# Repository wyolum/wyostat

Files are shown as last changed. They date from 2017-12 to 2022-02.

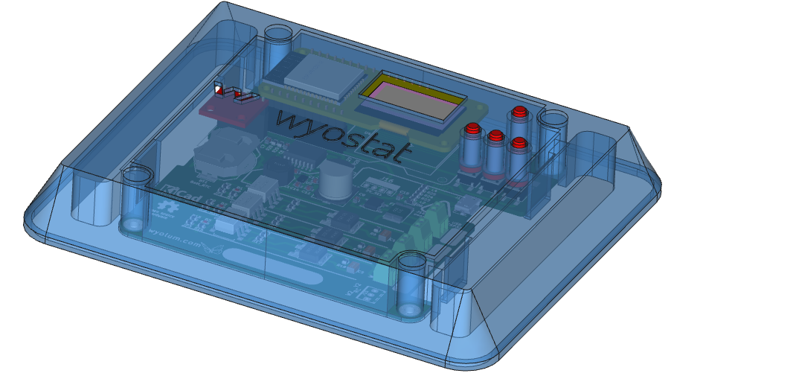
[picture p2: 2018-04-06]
fabricate/images/wyostat_fab_05.png

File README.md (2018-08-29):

# wyostat
Open source thermostat

* install node-red
           * https://nodered.org/docs/hardware/raspberrypi
* install node-red-dashboard
   	   * (from the ~/.node-red)
	   * https://flows.nodered.org/node/node-red-dashboard
* install node-red start up trigger: npm install node-red-contrib-startup-trigger
* install mosquitto (steps 1 & 2
           *https://learn.adafruit.com/diy-esp8266-home-security-with-lua-and-mqtt/configuring-mqtt-on-the-raspberry-pi)
* start node-red (from the command-line type $node-red)
* start mosquitto (from the command line type $moquitto)
* edit OpenThermostat.json from within node-red (update mqtt-broker ip address)
* deploy OpenThermostat.json from within node-red (update mqtt-broker ip address)
* Copy and edit arduino/OpenThermostat/README to arduino/OpenThermostat/config.h
* upload OpenThermostat.ino

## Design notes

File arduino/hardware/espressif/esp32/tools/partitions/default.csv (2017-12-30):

# Name | Type | SubType | Offset | Size | Flags
nvs | data | nvs | 0x9000 | 0x5000
otadata | data | ota | 0xe000 | 0x2000
app0 | app | ota_0 | 0x10000 | 0x140000
app1 | app | ota_1 | 0x150000 | 0x140000
eeprom | data | 0x99 | 0x290000 | 0x1000
spiffs | data | spiffs | 0x291000 | 0x16F000

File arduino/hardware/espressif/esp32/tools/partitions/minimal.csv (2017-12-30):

# Name | Type | SubType | Offset | Size | Flags
nvs | data | nvs | 0x9000 | 0x5000
otadata | data | ota | 0xe000 | 0x2000
app0 | app | ota_0 | 0x10000 | 0x140000
eeprom | data | 0x99 | 0x150000 | 0x1000
spiffs | data | spiffs | 0x151000 | 0xAF000

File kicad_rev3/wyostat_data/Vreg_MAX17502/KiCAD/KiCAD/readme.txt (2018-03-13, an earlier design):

 

**********************************************************
*************  Important Instructions Follow  ************
**********************************************************
 
All files exported to: C:\EMA\ExportFolder\0\175637\Output\KiCAD\KiCAD\symbols.lib

After you have used Ultra Librarian to export library:
**************************************************
**To import your new library symbols into KiCad:**
**************************************************
1. Open KiCad.
2. On the program/tool list, go to Eeschema.
3. Select *Preferences* from the menu bar then select *Library*.
4. Click *Add* and choose the newly exported *.LIB* file.
5. You have now successfully imported your new symbol library!

**************************************************************
**To import your new library footprints/patterns into KiCad:**
**************************************************************
1. Open KiCad.
2. On the program/tool list, go to Pcbnew.
3. Follow the same steps as you would importing symbols, only this time select the *.kicad_mod* file.
4. You have now successfully imported your new footprint/pattern.

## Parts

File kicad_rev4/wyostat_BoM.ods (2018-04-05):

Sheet: wyostat_pcb_BoM
No | Designator | Package | Quantity | Designation | Digi PN | Mfr. | Mfg PN | Decription | Link
1 | BT1 | CR2032_SMD | 1 | Batt_RTC | BK-912-ND | MPD (Memory Protection Devices) | BK-912 | HOLDER COIN CELL 20MM SMD | https://www.digikey.com/product-detail/en/mpd-memory-protection-devices/BK-912/BK-912-ND/2647825
2 | BATT1 | CR2032 | 1 | Battery Coin 2032 | P189-ND | Panasonic – BSG | CR2032 | BATTERY LITHIUM 3V COIN 20MM | https://www.digikey.com/product-detail/en/panasonic-bsg/CR2032/P189-ND/31939
3 | C1,C3,C5 | C_1210 | 3 | 10nF,120V | 399-12880-1-ND | KEMET | LDEIB2100KA0N00 | CAP FILM 10000PF 10% 250VDC 1210 | https://www.digikey.com/product-detail/en/kemet/LDEIB2100KA0N00/399-12880-1-ND/5731504
4 | C7,C8 | C_0805 | 2 | 100nF | 490-8049-1-ND | Murata Electronics North America | GCM21BR71H104KA37K | CAP CER 0.1UF 50V X7R 0805 | https://www.digikey.com/scripts/DkSearch/dksus.dll?Detail&itemSeq=255949432&uq=636584419937553153
5 | C9 | C_0805 | 1 | 100nF,100V | 1276-6733-1-ND | Samsung Electro-Mechanics | GCM21BR71H104KA37K | CAP CER 0.1UF 100V X7R 0805 | https://www.digikey.com/product-detail/en/samsung-electro-mechanics/CL21B104KCFWPNE/1276-6733-1-ND/5961592
6 | C10 | CP_Elec_10x10 | 1 | 100uF,50V | 565-4786-1-ND | United Chemi-Con | HHXC500ARA101MJA0G | CAP ALUM POLY 100UF 20% 50V SMD | https://www.digikey.com/product-detail/en/united-chemi-con/HHXC500ARA101MJA0G/565-4786-1-ND/7556757
7 | C11 | C_0805 | 1 | 2.2uF,50V | 587-4963-1-ND | Taiyo Yuden | UMK212BB7225MG-T | CAP CER 2.2UF 50V X7R 0805 | https://www.digikey.com/product-detail/en/taiyo-yuden/UMK212BB7225MG-T/587-4963-1-ND/6563806
8 | C12 | C_0805 | 1 | 1uF | 1276-1029-1-ND | Samsung Electro-Mechanics | CL21B105KBFNNNE | CAP CER 1UF 50V X7R 0805 | https://www.digikey.com/product-detail/en/samsung-electro-mechanics/CL21B105KBFNNNE/1276-1029-1-ND/3889115
9 | C13 | C_0805 | 1 | 3.3nF | 399-1153-1-ND | KEMET | C0805C332K5RACTU | CAP CER 3300PF 50V X7R 0805 | https://www.digikey.com/product-detail/en/kemet/C0805C332K5RACTU/399-1153-1-ND/411428
10 | C14 | C_0805 | 1 | 10uF | 587-3319-1-ND | Taiyo Yuden | EMK212BB7106MG-T | CAP CER 10UF 16V X7R 0805 | https://www.digikey.com/product-detail/en/taiyo-yuden/EMK212BB7106MG-T/587-3319-1-ND/4157364
11 | C15 | C_0805 | 1 | 4.7uF | 1276-2873-1-ND | Samsung Electro-Mechanics | CL21B475KOFNNNE | CAP CER 4.7UF 16V X7R 0805 | https://www.digikey.in/product-detail/en/samsung-electro-mechanics/CL21B475KOFNNNE/1276-2873-1-ND/3890959
12 | D1,D2,D3 | LED_0603 | 3 | LED | 160-1828-1-ND | Lite-On Inc. | LTST-C193KGKT-5A | LED GREEN CLEAR 0603 SMD | https://www.digikey.com/product-detail/en/lite-on-inc/LTST-C193KGKT-5A/160-1828-1-ND/2356247
13 | D4 | Diode_bridge | 1 | DiodeBridge | MDB6SFSCT-ND | ON Semiconductor | MDB6S | IC BRIDGE DIODE 600V 4-MICRODIP | https://www.digikey.com/product-detail/en/on-semiconductor/MDB6S/MDB6SFSCT-ND/3137112
14 | D5 | D_SOD-323_HandSoldering | 1 | CDSOD323-T05L | CDSOD323-T05LCT-ND | Bourns Inc. | CDSOD323-T05L | TVS DIODE 5V 18.3V SOD323 | https://www.digikey.com/product-detail/en/bourns-inc/CDSOD323-T05L/CDSOD323-T05LCT-ND/5355715
15 | F1 | Fuse_SMD2920 | 1 | Polyfuse | 507-1743-1-ND | Bel Fuse Inc. | 0ZCF0075AF2C | PTC RESET FUSE 60V 750MA 2920 | https://www.digikey.com/product-detail/en/bel-fuse-inc/0ZCF0075AF2C/507-1743-1-ND/4156174
16 | J1,J2,J3,J4 | TerminalBlock_Pheonix_MPT-2.54mm_2pol | 4 | 24VAC IN,OUT1,OUT2,OUT3 | A98333-ND | TE Connectivity AMP Connectors | 282834-2 | TERM BLOCK 2POS SIDE ENT 2.54MM | https://www.digikey.com/product-detail/en/te-connectivity-amp-connectors/282834-2/A98333-ND/1150135
17 | J13 | USB_Micro-B_Molex-105017-0001 | 1 | USB_microAB | WM1399CT-ND | Molex, LLC | 1050170001 | CONN RCPT MICRO USB R/A SMD | https://www.digikey.com/product-detail/en/molex-llc/1050170001/WM1399CT-ND/2350885
18 | J16 | Pin_Header_Straight_1x04 | 1 | 5V_SEL | S1011EC-04-ND | Sullins Connector Solutions | PRPC004SAAN-RC | CONN HEADER .100" SNGL STR 4POS | https://www.digikey.com/product-detail/en/sullins-connector-solutions/PRPC004SAAN-RC/S1011EC-04-ND/2775250
19 | JP1,JP2,JP3 | R_0805 | 3 | LED_en | YAG3755CT-ND | Yageo | AC0805JR-070RL | RES SMD 0 OHM JUMPER 1/8W 0805 | https://www.digikey.com/product-detail/en/yageo/AC0805JR-070RL/YAG3755CT-ND/6006604
20 | Shorting link for J16 | -- | 1 | -- | S9337-ND | Sullins Connector Solutions | QPC02SXGN-RC | CONN JUMPER SHORTING .100" GOLD | https://www.digikey.com/product-detail/en/sullins-connector-solutions/QPC02SXGN-RC/S9337-ND/2618262
21 | L1 | Inductor_ELL8TP | 1 | 22uH | PCD2446CT-ND | Panasonic Electronic Components | ELL-8TP220MB | FIXED IND 22UH 2A 55 MOHM SMD | https://www.digikey.com/product-detail/en/panasonic-electronic-components/ELL-8TP220MB/PCD2446CT-ND/5673833
22 | L2,L4 | R_0805 | 2 | 330E | 445-1569-1-ND | TDK Corporation | MPZ2012S331AT000 | FERRITE BEAD 330 OHM 0805 1LN | https://www.digikey.com/product-detail/en/tdk-corporation/MPZ2012S331AT000/445-1569-1-ND/571899
23 | Q1,Q2,Q3 | DPAK-2 | 3 | BTA204S | 1740-1106-1-ND | WeEn Semiconductors | BTA204S-600E,118 | TRIAC SENS GATE 600V 4A DPAK | https://www.digikey.com/product-detail/en/ween-semiconductors/BTA204S-600E118/1740-1106-1-ND/2531110
24 | R1,R5,R7,R12,R13,R17 | R_0805 | 6 | 360 | 311-360CRCT-ND | Yageo | RC0805FR-07360RL | RES SMD 360 OHM 1% 1/8W 0805 | https://www.digikey.com/product-detail/en/yageo/RC0805FR-07360RL/311-360CRCT-ND/730833
25 | R3,R9,R15 | R_0805 | 3 | 200 | 311-200ARCT-ND | Yageo | RC0805JR-07200RL | RES SMD 200 OHM 5% 1/8W 0805 | https://www.digikey.com/product-detail/en/yageo/RC0805JR-07200RL/311-200ARCT-ND/731226
26 | R4,R10,R16 | R_0805 | 3 | 300 | 311-300ARCT-ND | Yageo | RC0805JR-07300RL | RES SMD 300 OHM 5% 1/8W 0805 | https://www.digikey.com/product-detail/en/yageo/RC0805JR-07300RL/311-300ARCT-ND/731254
27 | R6,R11,R18 | R_0805 | 3 | 39 | 311-39ARCT-ND | Yageo | RC0805JR-0739RL | RES SMD 39 OHM 5% 1/8W 0805 | https://www.digikey.com/product-detail/en/yageo/RC0805JR-0739RL/311-39ARCT-ND/731268
28 | R19,R20,R21,R22,R26,R27 | R_0805 | 6 | 10k | 311-10KARCT-ND | Yageo | RC0805JR-0710KL | RES SMD 10K OHM 5% 1/8W 0805 | https://www.digikey.com/product-detail/en/yageo/RC0805JR-0710KL/311-10KARCT-ND/731188
29 | R28,R29 | R_0805 | 2 | 4K7 | 311-4.70KCRCT-ND | Yageo | RC0805FR-074K7L | RES SMD 4.7K OHM 1% 1/8W 0805 | https://www.digikey.com/product-detail/en/yageo/RC0805FR-074K7L/311-4.70KCRCT-ND/730876
30 | S1,S2,S3,S4 | SW_SPST_FSM6JSMA | 4 | SW-ENTER,SW-INC,SW-DEC,SW-MODE | 450-1133-ND | TE Connectivity ALCOSWITCH Switches | FSM6JSMA | SWITCH TACTILE SPST-NO 0.05A 24V | https://www.digikey.com/product-detail/en/te-connectivity-alcoswitch-switches/FSM6JSMA/450-1133-ND/525822
31 | U1,U2,U3 | Optocoupler_6pin_smd | 3 | MOC3063M | MOC3063SR2MCT-ND | ON Semiconductor | MOC3063SR2M | OPTOISOLATOR 4.17KV TRIAC 6SMD | https://www.digikey.com/product-detail/en/on-semiconductor/MOC3063SR2M/MOC3063SR2MCT-ND/1626439
32 | U4 | Wemos_Lolin | 1 | Wemos-Lolin
33 | U5 | TDFN-10 | 1 | MAX17502FATB+T | MAX17502FATB+TCT-ND | Maxim Integrated | MAX17502FATB+T | IC REG BUCK 5V 1A SYNC 10TDFN | https://www.digikey.com/product-detail/en/maxim-integrated/MAX17502FATB-T/MAX17502FATB-TCT-ND/4807778
34 | U130 | DS3231 | 1 | DS3231N | DS3231M+-ND | Maxim Integrated | DS3231M+ | IC RTC CLK/CALENDAR I2C 16-SOIC | https://www.digikey.com/product-detail/en/maxim-integrated/DS3231M/DS3231M-ND/2402420

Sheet: BoM_SCH
Quantity | Reference | Value | DNP
1 | BT1, | Batt_RTC
3 | C1,C3,C5, | 10nF,120V
2 | C7,C8, | 100nF
1 | C9, | 100nF,100V
1 | C10, | 100uF,50V
1 | C11, | 2.2uF,50V
1 | C12, | 1uF
1 | C13, | 3.3nF
1 | C14, | 10uF
1 | C15, | 4.7uF
3 | D1,D2,D3, | LED
1 | D4, | DiodeBridge
1 | D5, | CDSOD323-T05L
1 | F1, | Polyfuse
1 | J1, | 24 V AC IN
1 | J2, | OUT1
1 | J3, | OUT2
1 | J4, | OUT3
1 | J13, | USB_microAB
1 | J16, | 5V_SEL
3 | JP1,JP2,JP3, | LED_en
1 | L1, | 22uH
2 | L2,L4, | 330E
3 | Q1,Q2,Q3, | BTA204S
6 | R1,R5,R7,R12,R13,R17, | 360
3 | R3,R9,R15, | 200
3 | R4,R10,R16, | 300
3 | R6,R11,R18, | 39 | -
6 | R19,R20,R21,R22,R26,R27, | 10k
2 | R28,R29, | 4K7
1 | S1, | SW-ENTER
1 | S2, | SW-INC
1 | S3, | SW-DEC
1 | S4, | SW-MODE
3 | U1,U2,U3, | MOC3063M
1 | U4, | Wemos-Lolin
1 | U5, | MAX17502FATB+T
1 | U6, | DS3231N
1 | J5, | I2C_ext1
1 | J6, | RH
1 | J7, | RC
1 | J8, | C
1 | J9, | Y1
1 | J10, | Y2
1 | J11, | G
1 | J12, | W1
1 | J14, | W2
1 | J15, | Conn_Spare
1 | JP4, | GND
1 | Logo1, | LOGO_WL
1 | Logo2, | OSHW
1 | Logo3, | KiCad
1 | Logo4, | logo_snb
1 | Logo5, | logo_warning
3 | R23,R24,R25, | 0E | DNP
4 | SC1,SC2,SC3,SC4, | SCREW
1 | TP1, | ~RST
1 | TP2, | SQR
1 | TP3, | 32kHz

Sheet: BoM_PCB
Id | Designator | Package | Quantity | Designation | Supplier and ref
1 | BT1 | CR2032_SMD2 | 1 | Batt_RTC
2 | C1,C3,C5 | C_1210 | 3 | 10nF,120V
3 | C7,C8 | C_0805 | 2 | 100nF
4 | C9 | C_0805 | 1 | 100nF,100V
5 | C10 | CP_Elec_10x10 | 1 | 100uF,50V
6 | C11 | C_0805 | 1 | 2.2uF,50V
7 | C12 | C_0805 | 1 | 1uF
8 | C13 | C_0805 | 1 | 3.3nF
9 | C14 | C_0805 | 1 | 10uF
10 | C15 | C_0805 | 1 | 4.7uF
11 | D1,D2,D3 | LED_0603 | 3 | LED
12 | D4 | Diode_bridge | 1 | DiodeBridge
13 | D5 | D_SOD-323_HandSoldering | 1 | CDSOD323-T05L
14 | F1 | Fuse_SMD2920 | 1 | Polyfuse
15 | J1 | TerminalBlock_Pheonix_MPT-2.54mm_2pol | 1 | 24 V AC IN
 | J2 | TerminalBlock_Pheonix_MPT-2.54mm_2pol | 1 | OUT1
 | J3 | TerminalBlock_Pheonix_MPT-2.54mm_2pol | 1 | OUT2
 | J4 | TerminalBlock_Pheonix_MPT-2.54mm_2pol | 1 | OUT3
16 | J13 | USB_Micro-B_Molex-105017-0001 | 1 | USB_microAB
17 | J16 | Pin_Header_Straight_1x04 | 1 | 5V_SEL
18 | JP1,JP2,JP3 | R_0805 | 3 | LED_en
19 | L1 | Inductor_ELL8TP | 1 | 22uH
20 | L2,L4 | R_0805 | 2 | 330E
21 | Q1,Q2,Q3 | DPAK-2 | 3 | BTA204S
22 | R1,R5,R7,R12,R13,R17 | R_0805 | 6 | 360
23 | R3,R9,R15 | R_0805 | 3 | 200
24 | R4,R10,R16 | R_0805 | 3 | 300
25 | R6,R11,R18 | R_0805 | 3 | 39
26 | R19,R20,R21,R22,R26,R27 | R_0805 | 6 | 10k
27 | R28,R29 | R_0805 | 2 | 4K7
28 | S1 | SW_SPST_FSM6JSMA | 1 | SW-ENTER
 | S2 | SW_SPST_FSM6JSMA | 1 | SW-INC
 | S3 | SW_SPST_FSM6JSMA | 1 | SW-DEC
 | S4 | SW_SPST_FSM6JSMA | 1 | SW-MODE
29 | U1,U2,U3 | Optocoupler_6pin_smd | 3 | MOC3063M
30 | U4 | Wemos_Lolin | 1 | Wemos-Lolin
31 | U5 | TDFN-10 | 1 | MAX17502FATB+T
32 | U6 | DS3231 | 1 | DS3231N
33 | J5 | Pin_Header_Straight_1x04 | 1 | I2C_ext1
34 | J6 | pad_rect_smd | 1 | RH
 | J7 | pad_rect_smd | 1 | RC
 | J8 | pad_rect_smd | 1 | C
 | J9 | pad_rect_smd | 1 | Y1
 | J10 | pad_rect_smd | 1 | Y2
 | J11 | pad_rect_smd | 1 | G
 | J12 | pad_rect_smd | 1 | W1
 | J14 | pad_rect_smd | 1 | W2
35 | J15 | TerminalBlock_Pheonix_MPT-2.54mm_3pol | 1 | Conn_Spare
36 | JP4 | LED_0402 | 1 | GND
37 | Logo1 | logo-WL3 | 1 | LOGO_WL
38 | Logo2 | logo-OSHW_6mm | 1 | OSHW
39 | Logo3 | logo-kicad_6mm_SilkScreen | 1 | KiCad
40 | Logo4 | logo-skull_n_bones | 1 | logo_snb
41 | Logo5 | logo-warning | 1 | logo_warning
42 | R23,R24,R25 | R_0805 | 3 | 0E
43 | SC1,SC2,SC3,SC4 | MountingHole_3.2mm_M3_Pad_Via | 4 | SCREW
44 | TP1 | Pin_Header_Straight_1x01 | 1 | ~RST
 | TP2 | Pin_Header_Straight_1x01 | 1 | SQR
 | TP3 | Pin_Header_Straight_1x01 | 1 | 32kHz

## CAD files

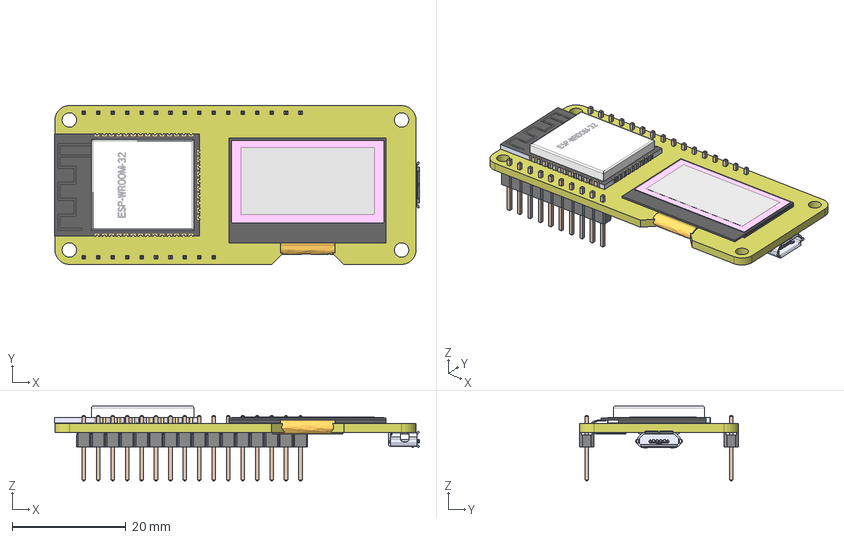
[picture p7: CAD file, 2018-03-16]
fabricate/wemos/wemos.step
64.2 x 27.9 x 13.1 mm
pin_header_01x10
pin_header_01x16
MicroUSB-B_Molex_105017-0001
esp-wroom-32
Clone_of_ER_OLED013A1_inv

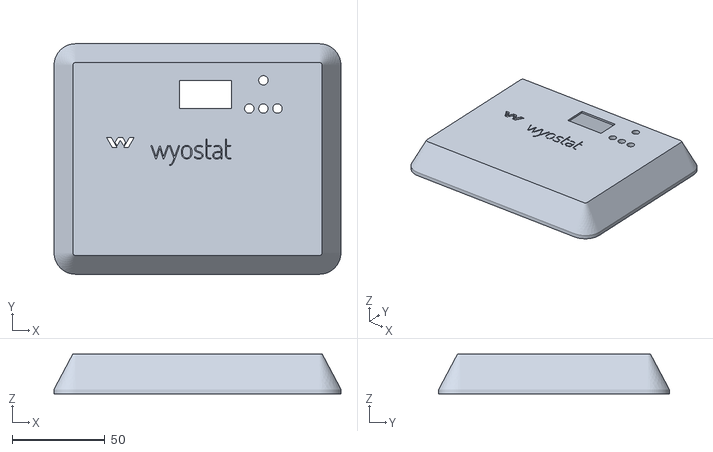
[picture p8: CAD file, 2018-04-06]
fabricate/wyostat_cover.stl
154.9 x 124.5 x 21.6

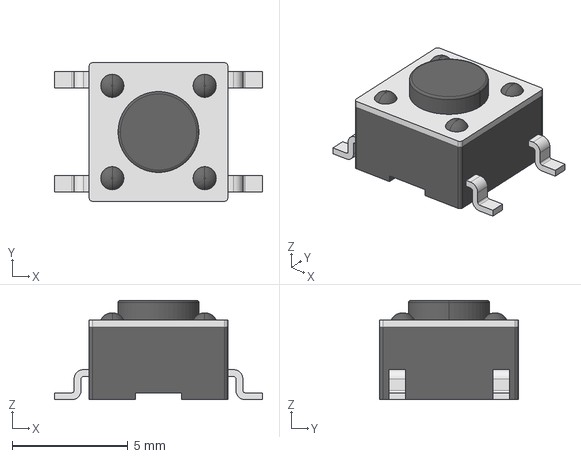
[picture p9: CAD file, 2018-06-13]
kicad_rev4/wyostat_3d_modules/sw_pb_smd.step
9.00 x 6.00 x 4.30 mm

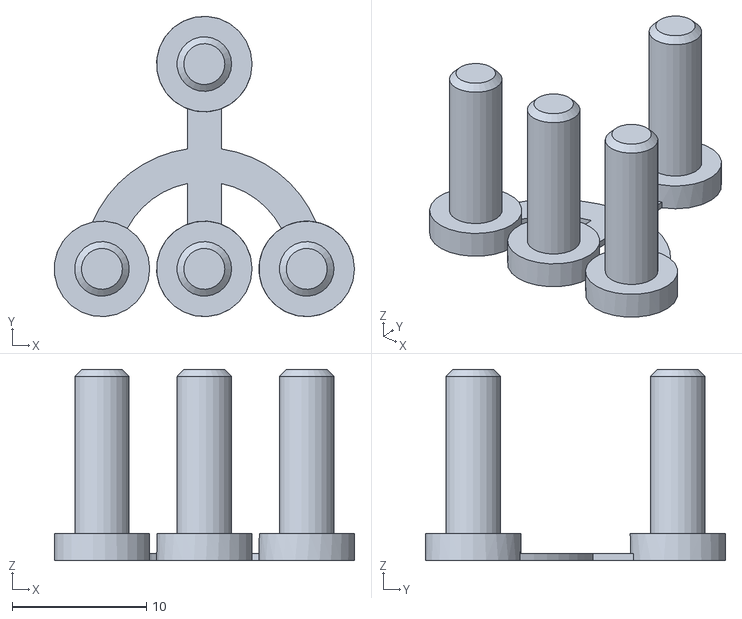
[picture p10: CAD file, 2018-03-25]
fabricate/wyostat_buttons.stl
22.3 x 22.3 x 14.2

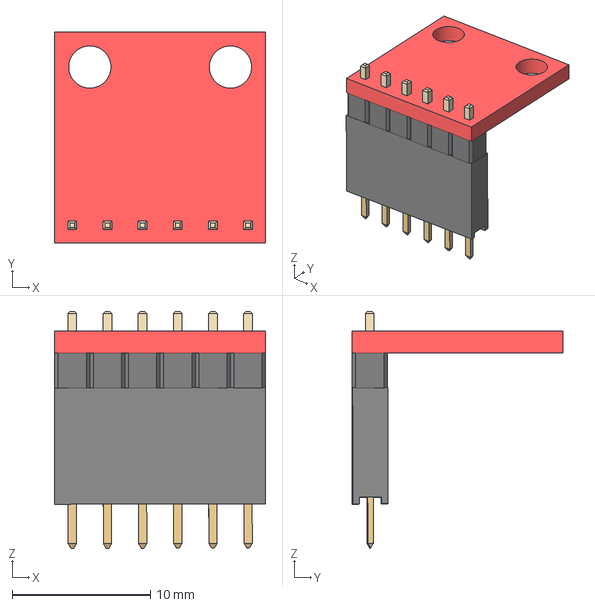
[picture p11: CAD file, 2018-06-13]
kicad_rev4/wyostat_3d_modules/sparkfun_TMP102.step
15.3 x 15.3 x 17.1 mm

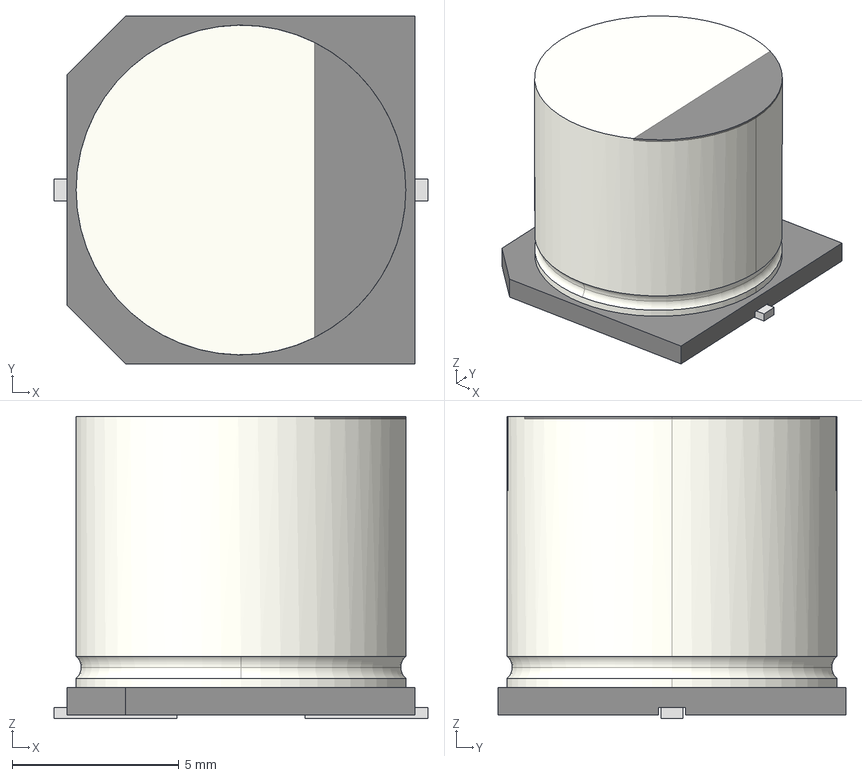
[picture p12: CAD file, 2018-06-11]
kicad_rev4/wyostat_3d_modules/cap_elco_10x10x10.step
11.2 x 10.4 x 9.07 mm

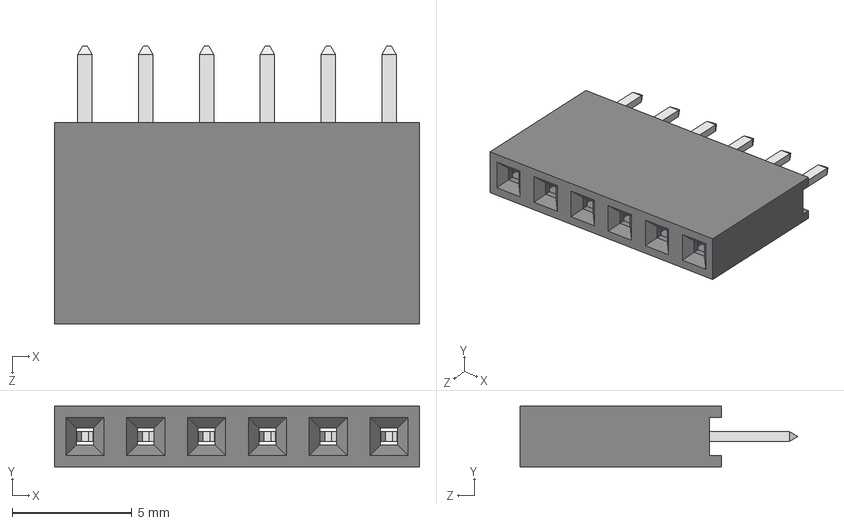
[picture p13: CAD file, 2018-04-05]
kicad_rev4/wyostat_3d_modules/pin_header_female_01x06.step
15.2 x 2.54 x 11.6 mm

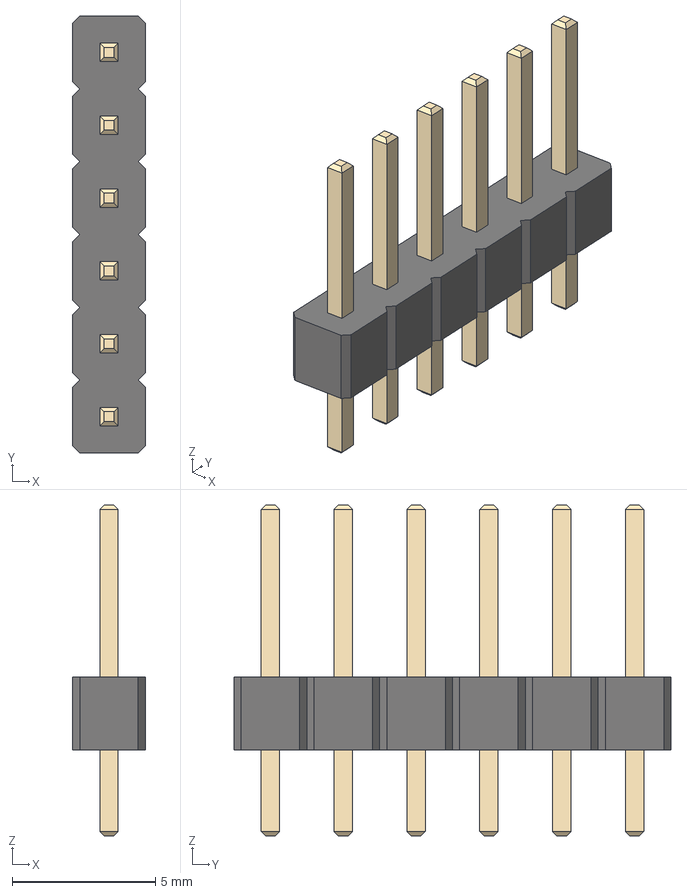
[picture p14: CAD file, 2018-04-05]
kicad_rev4/wyostat_3d_modules/Pin_Header_Straight_1x06_Pitch2.54mm.step
2.54 x 15.2 x 11.5 mm

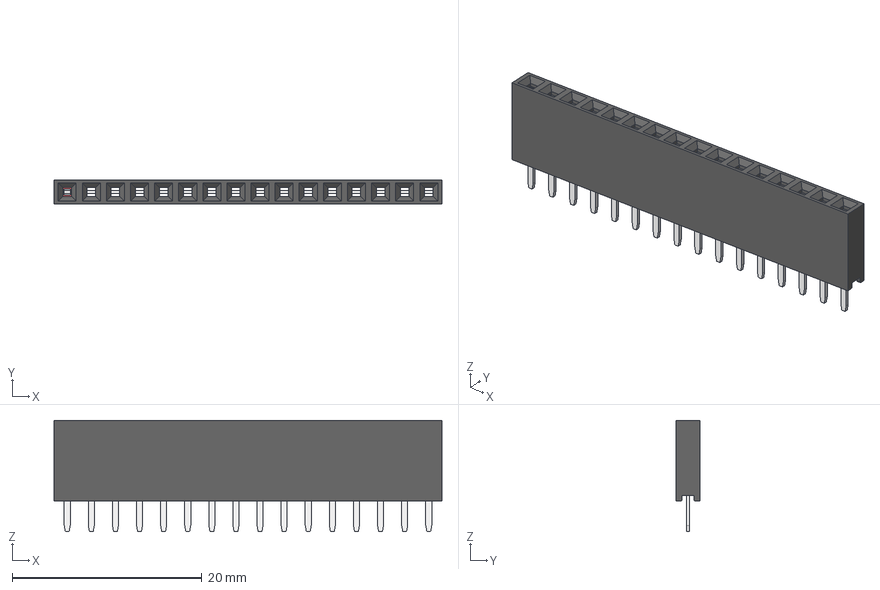
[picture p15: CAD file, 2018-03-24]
kicad_rev4/wyostat_3d_modules/Header_F16x2-54.step
40.9 x 2.50 x 11.7 mm

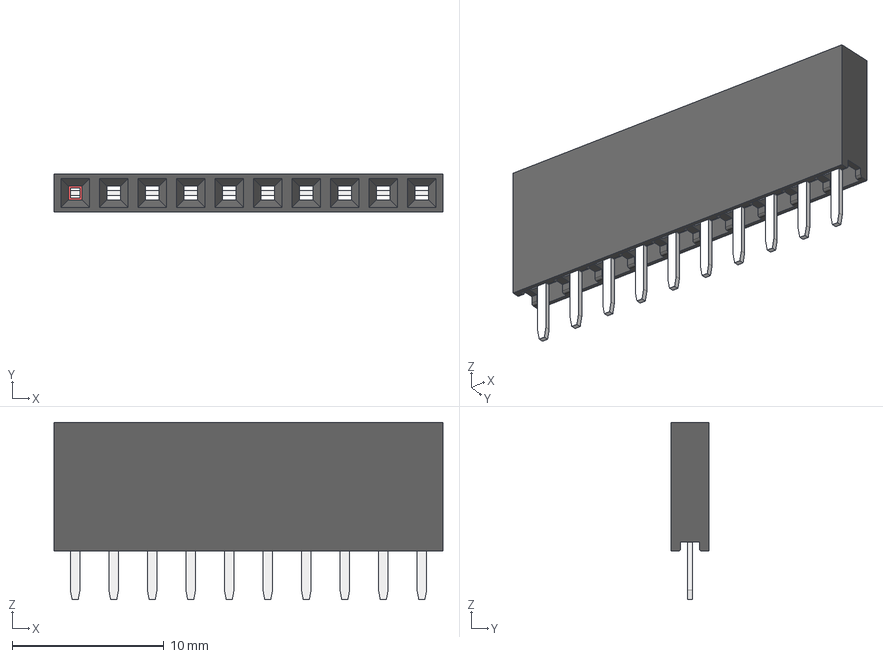
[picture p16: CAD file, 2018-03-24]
kicad_rev4/wyostat_3d_modules/Header_F_10x2_54.step
25.6 x 2.50 x 11.7 mm

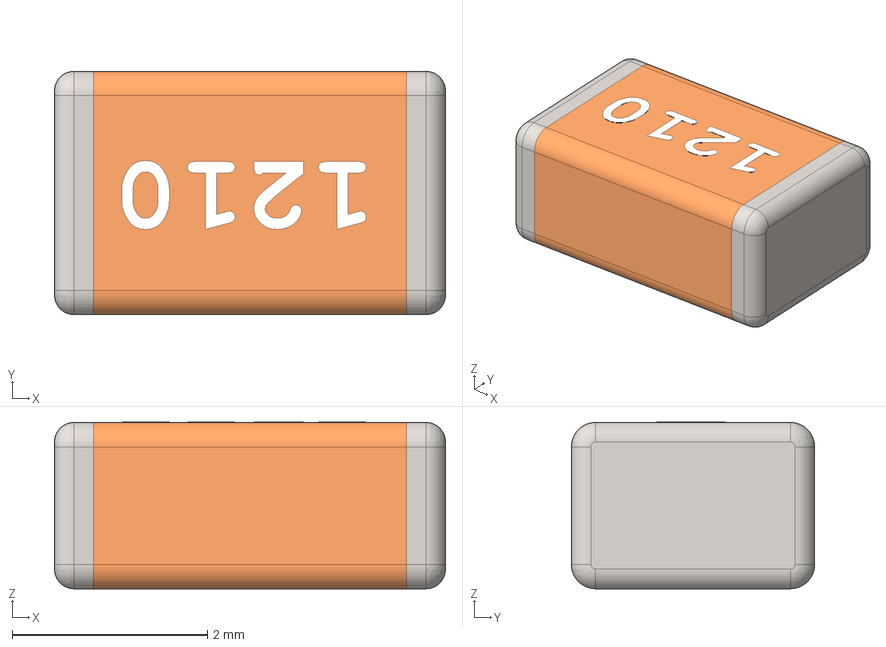
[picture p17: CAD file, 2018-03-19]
kicad_rev4/wyostat_3d_modules/cap_1210_3225M.step
4.00 x 2.49 x 1.70 mm

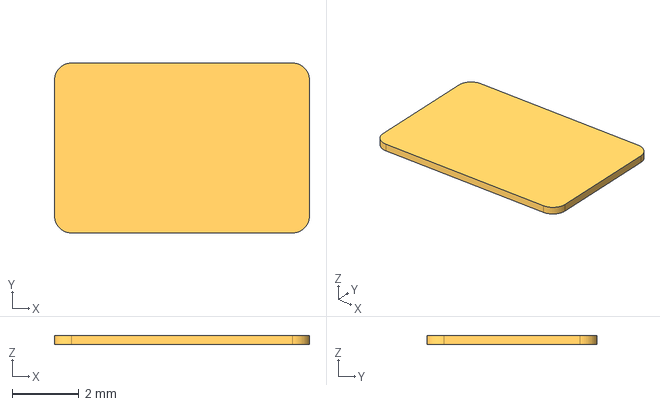
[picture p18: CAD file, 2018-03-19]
kicad_rev4/wyostat_3d_modules/pad_rect_smd.step
7.62 x 5.08 x 0.254 mm

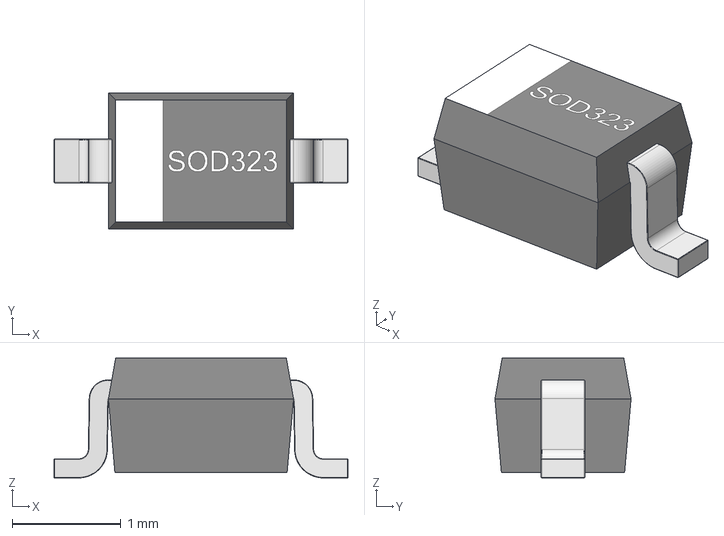
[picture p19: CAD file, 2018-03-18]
kicad_rev4/wyostat_3d_modules/D_SOD323.step
2.70 x 1.25 x 1.10 mm

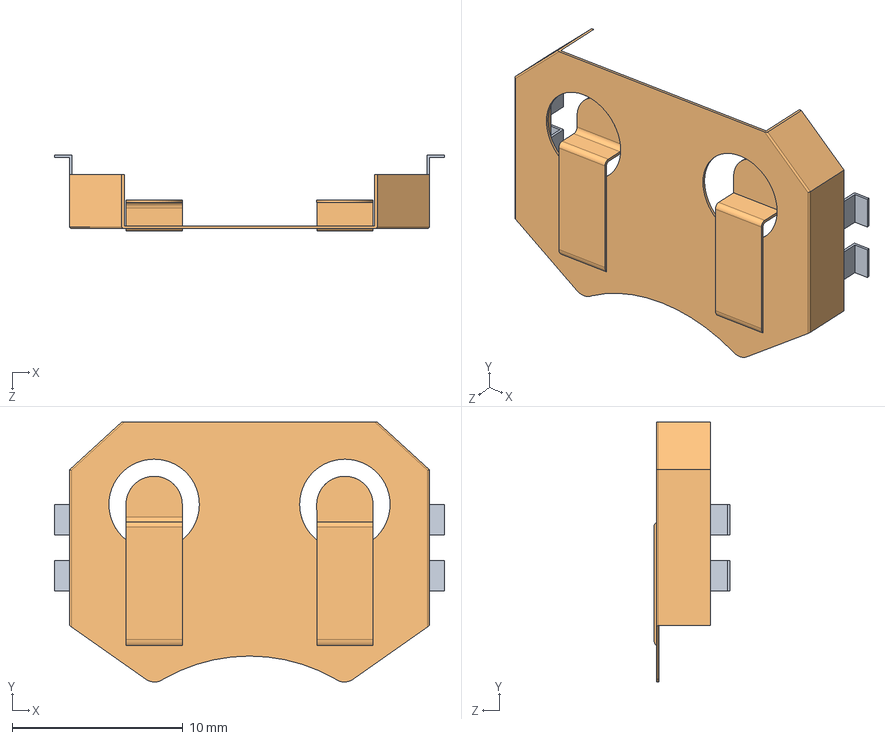
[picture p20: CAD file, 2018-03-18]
kicad_rev4/wyostat_3d_modules/bat_2032_BK-912_V1I3.step
22.9 x 15.2 x 4.47 mm
User Library-BK-912_V1I3_1
User Library-BK-912_V1I3_2
User Library-BK-912_V1I3_3
User Library-BK-912_V1I3_4
User Library-BK-912_V1I3_5

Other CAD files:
fabricate/wemos/lolin_01.fcstd
kicad_rev4/wyostat_3d_modules/bat_cr2032.step
kicad_rev4/wyostat_3d_modules/SOIC16_Wide.step
kicad_rev4/wyostat_3d_modules/bat_2032_2.step
kicad_rev3/wyostat_3d_modules/Conn_Phoenix_MPT.step
kicad_rev3/wyostat_3d_modules/MicroUSB-B_Molex_105017-0001.step
kicad_rev3/wyostat_3d_modules/SOIC16_Wide.step
kicad_rev3/wyostat_3d_modules/SOT-428.step
kicad_rev3/wyostat_3d_modules/SW_SPST_CK_KSCx.step
kicad_rev3/wyostat_3d_modules/TDFN10.step
kicad_rev3/wyostat_3d_modules/bat_2032_2.step
kicad_rev3/wyostat_3d_modules/bat_cr2032.step
kicad_rev3/wyostat_3d_modules/cap_0805_2012M.step
kicad_rev3/wyostat_3d_modules/cap_2220_5750M.step
kicad_rev3/wyostat_3d_modules/cap_2917_7343M.step
kicad_rev3/wyostat_3d_modules/cap_elco_EEE_G-L.step
kicad_rev3/wyostat_3d_modules/cap_elco_EEE_G-M.step
kicad_rev3/wyostat_3d_modules/cap_elco_EEE_G.step
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

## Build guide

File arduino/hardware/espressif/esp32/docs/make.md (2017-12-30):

To use make
============

 [makeEspArduino](https://github.com/plerup/makeEspArduino) is a generic makefile for any ESP8266/ESP32 Arduino project.Using make instead of the Arduino IDE makes it easier to do automated and production builds.

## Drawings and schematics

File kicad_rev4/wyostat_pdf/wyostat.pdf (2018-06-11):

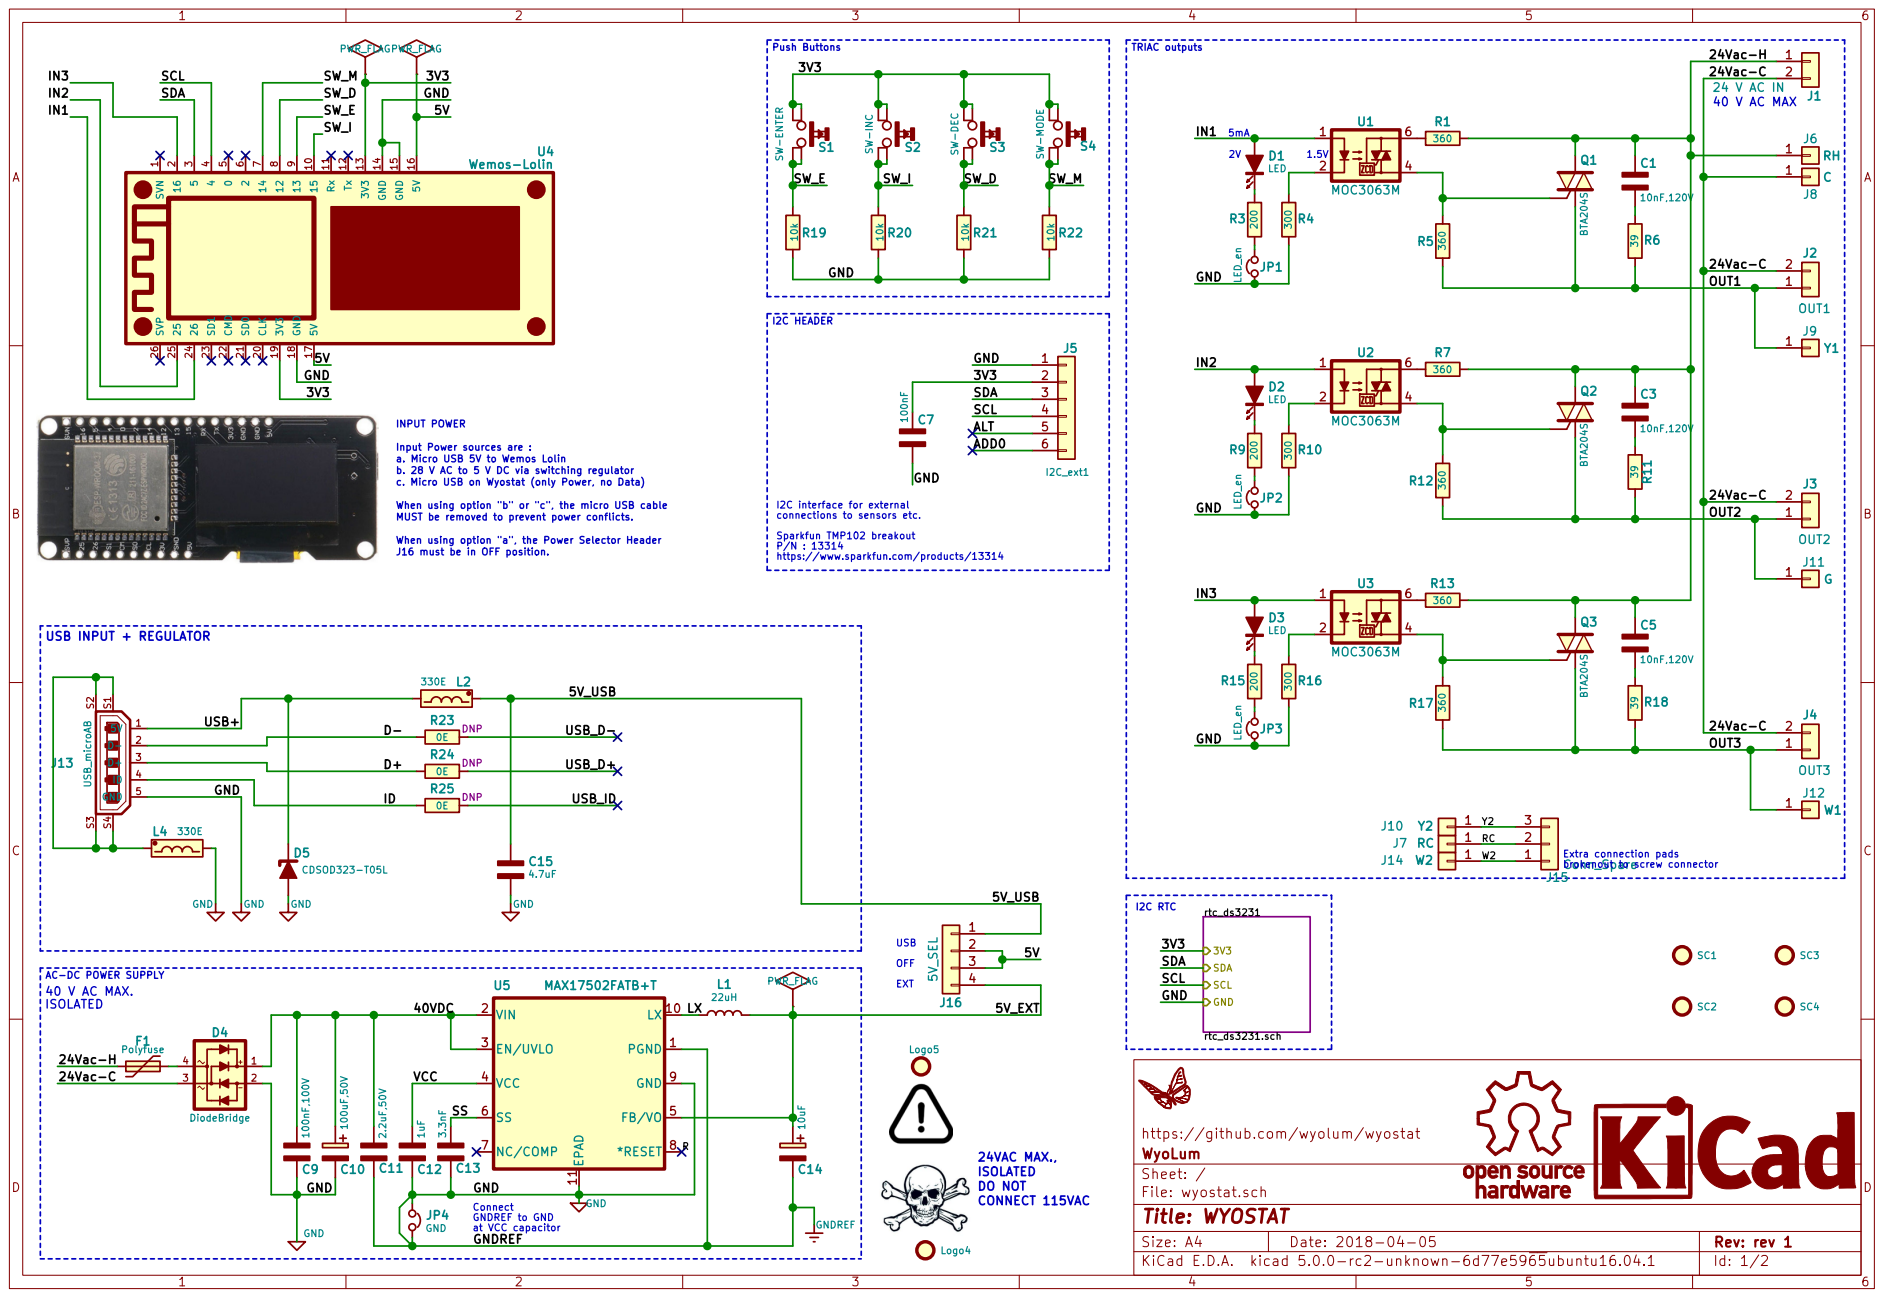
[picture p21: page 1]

6 U1 MOC3063M

1 15 10 Rx 11 Tx 12 3V3 13 GND 14 GND 15 5V 16 5V 17 GND 18 3V3 19 16

b. 28 V AC to 5 V DC via switching regulator c. Micro USB on Wyostat (only Power, no Data) When using option "b" or "c", the micro USB cable MUST be removed to prevent power conflicts. When using option "a", the Power Selector Header J16 must be in OFF position. VCC

Input Power sources are : a. Micro USB 5V to Wemos Lolin

I2C interface for external connections to sensors etc. Sparkfun TMP102 breakout P/N : 13314

https://www.sparkfun.com/products/13314

6 U3 MOC3063M

USB INPUT + REGULATOR

Extra connection pads brokenout to screw connector

https://github.com/wyolum/wyostat
File: wyostat.sch Sheet: / WyoLum

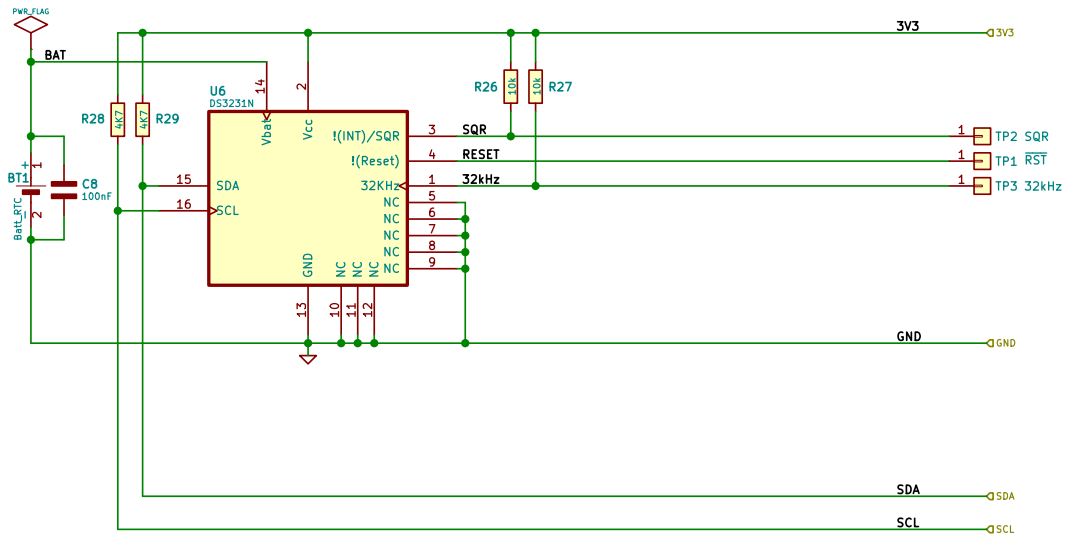
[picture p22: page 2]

https://github.com/wyolum/wyostat
WyoLum
Sheet: /rtc_ds3231/
File: rtc_ds3231.sch
Id: 2/2 Title: WYOSTAT

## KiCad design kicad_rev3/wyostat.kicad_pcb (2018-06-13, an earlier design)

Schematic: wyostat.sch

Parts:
C1, C3, C5: 10nF,120V; C_1210
C7: 100nF; C_0805
C9: 100nF,100V; C_0805
C10: 100uF,50V; CP_Elec_10x10
C11: 2.2uF,50V; C_0805
C12: 1uF; C_0805
C13: 3.3nF; C_0805
C14: 10uF; C_0805
C15: 4.7uF; C_0805
D1, D2, D3: LED; LED_0603
D4: DiodeBridge; Diode_bridge
D5: CDSOD323-T05L; D_SOD-323_HandSoldering
F1: Polyfuse; Fuse_SMD2920
J1: 24 V AC IN; TerminalBlock_Pheonix_MPT-2.54mm_2pol
J2: OUT1; TerminalBlock_Pheonix_MPT-2.54mm_2pol
J3: OUT2; TerminalBlock_Pheonix_MPT-2.54mm_2pol
J4: OUT3; TerminalBlock_Pheonix_MPT-2.54mm_2pol
J5: I2C_ext1; Pin_Header_TMP102_1x06
J6: RH; pad_rect_smd
J7: RC; pad_rect_smd
J8: C; pad_rect_smd
J9: Y1; pad_rect_smd
J10: Y2; pad_rect_smd
J11: G; pad_rect_smd
J12: W1; pad_rect_smd
J13: USB_microAB; USB_Micro-B_Molex-105017-0001
J14: W2; pad_rect_smd
J15: Conn_Spare; TerminalBlock_Pheonix_MPT-2.54mm_3pol
J16: 5V_SEL; Pin_Header_Straight_1x04
JP1, JP2, JP3: LED_en; R_0805
JP4: GND; LED_0402
L1: 22uH; Inductor_ELL8TP
L2, L4: 330E; R_0805
Logo1: LOGO_WL; logo-WL3
Logo2: OSHW; logo-OSHW_6mm
Logo3: KiCad; logo-kicad_6mm_SilkScreen
Logo4: logo_snb; logo-skull_n_bones
Logo5: logo_warning; logo-warning
Q1, Q2, Q3: BTA204S; DPAK-2
R1, R5, R7, R12, R13, R17: 360; R_0805
R3, R9, R15: 200; R_0805
R4, R10, R16: 300; R_0805
R6, R11, R18: 39; R_0805
R19, R20, R21, R22: 10k; R_0805
R23, R24, R25: 0E; R_0805
S1: SW-ENTER; SW_SPST_FSM6JSMA
S2: SW-INC; SW_SPST_FSM6JSMA
S3: SW-DEC; SW_SPST_FSM6JSMA
S4: SW-MODE; SW_SPST_FSM6JSMA
SC1, SC2, SC3, SC4: SCREW; MountingHole_3.2mm_M3_Pad_Via
U1, U2, U3: MOC3063M; Optocoupler_6pin_smd
U4: Wemos-Lolin; Wemos_Lolin
U5: MAX17502FATB+T; TDFN-10

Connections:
/3V3: C7.2, J5.2, S1.1, S1.3, S2.1, S2.3, S3.1, S3.3, S4.2, S4.4, U4.13, U4.19; also elsewhere on the board
/5V: J16.2, J16.3, U4.16, U4.17
/5V_EXT: C14.1, J16.4, L1.2, U5.5
/5V_USB: C15.1, J16.1, L2.1
/24Vac-C: D4.3, J1.2, J2.2, J3.2, J4.2, J8.1
/24Vac-H: C1.2, C3.2, C5.2, F1.2, J1.1, J6.1, Q1.2 (T2), Q2.2 (T2), Q3.2 (T2), R1.2, R7.2, R13.2
/40VDC: C9.1, C10.1, C11.2, D4.1, U5.2, U5.3
/D+: J13.3, R24.2
/D-: J13.2, R23.2
/ID: J13.4, R25.2
/IN1: D1.1, U1.1, U4.24
/IN2: D2.1, U2.1, U4.25
/IN3: D3.1, U3.1, U4.2
/LX: L1.1, U5.10
/OUT1: J2.1, J9.1, Q1.1 (T1), R5.2, R6.1
/OUT2: J3.1, J11.1, Q2.1 (T1), R11.1, R12.2
/OUT3: J4.1, J12.1, Q3.1 (T1), R17.2, R18.1
/RC: J7.1, J15.2
/SCL: J5.4, U4.4; also elsewhere on the board
/SDA: J5.3, U4.3; also elsewhere on the board
/SS: C13.2, U5.6
/SW_D: R21.1, S3.2, S3.4, U4.8
/SW_E: R19.1, S1.2, S1.4, U4.9
/SW_I: R20.1, S2.2, S2.4, U4.10
/SW_M: R22.1, S4.1, S4.3, U4.7
/USB+: D5.1 (K), J13.1, L2.2
/VCC: C12.1, U5.4
/W2: J14.1, J15.1
/Y2: J10.1, J15.3
GND: C7.1, C9.2, C10.2, C11.1, C12.2, C13.1, C14.2, C15.2, D4.2, D5.2 (A), J5.1, J13.5, JP1.2, JP2.2, JP3.2, JP4.1, JP4.2, L4.2, R4.1, R10.1, R16.1, R19.2, R20.2, R21.2, R22.2, U4.14, U4.15, U4.18, U5.1, U5.9, U5.11; also elsewhere on the board
unnamed: C1.1, R6.2
unnamed: C3.1, R11.2
unnamed: C5.1, R18.2
unnamed: D1.2, R3.2
unnamed: D2.2, R9.2
unnamed: D3.2, R15.2
unnamed: D4.4, F1.1
unnamed: J13.S1, J13.S2, J13.S3, J13.S4, L4.1
unnamed: JP1.1, R3.1
unnamed: JP2.1, R9.1
unnamed: JP3.1, R15.1
unnamed: Q1.3 (G), R5.1, U1.4
unnamed: Q2.3 (G), R12.1, U2.4
unnamed: Q3.3 (G), R17.1, U3.4
unnamed: R1.1, U1.6
unnamed: R4.2, U1.2
unnamed: R7.1, U2.6
unnamed: R10.2, U2.2
unnamed: R13.1, U3.6
unnamed: R16.2, U3.2

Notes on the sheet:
Push Buttons
I2C interface for external connections to sensors etc. Sparkfun TMP102 breakout P/N : 13314 https://www.sparkfun.com/products/13314
I2C HEADER
TRIAC outputs
1.5V
Connect GNDREF to GND at VCC capacitor
AC-DC POWER SUPPLY
40 V AC MAX. ISOLATED
40 V AC MAX
INPUT POWER Input Power sources are : a. Micro USB 5V to Wemos Lolin b. 28 V AC to 5 V DC via switching regulator c. Micro USB on Wyostat (only Power, no Data) When using option "b" or "c", the micro USB cable MUST be removed to prevent power conflicts. When using option "a", the Power Selector Hea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
USB INPUT + REGULATOR
5mA
I2C RTC
24VAC MAX., ISOLATED DO NOT CONNECT 115VAC
USB OFF EXT
Extra connection pads brokenout to screw connector

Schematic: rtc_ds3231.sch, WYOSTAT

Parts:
BT1: Batt_RTC; CR2032_SMD2; Digikey BU2032SM-HD-GCT-ND
C8: 100nF; C_0805
R26, R27: 10k; R_0805
R28, R29: 4K7; R_0805
TP1: ~RST; Pin_Header_Straight_1x01
TP2: SQR; Pin_Header_Straight_1x01
TP3: 32kHz; Pin_Header_Straight_1x01
U6: DS3231N; DS3231

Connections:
/3V3: R26.1, R27.1, R28.2, R29.2, U6.2; also elsewhere on the board
/SCL: R28.1, U6.16; also elsewhere on the board
/SDA: R29.1, U6.15; also elsewhere on the board
/rtc_ds3231/32kHz: R27.2, TP3.1, U6.1
/rtc_ds3231/BAT: BT1.1, C8.1, U6.14
/rtc_ds3231/RESET: TP1.1, U6.4
/rtc_ds3231/SQR: R26.2, TP2.1, U6.3
GND: BT1.2, C8.2, U6.5, U6.6, U6.7, U6.8, U6.9, U6.10, U6.11, U6.12, U6.13; also elsewhere on the board

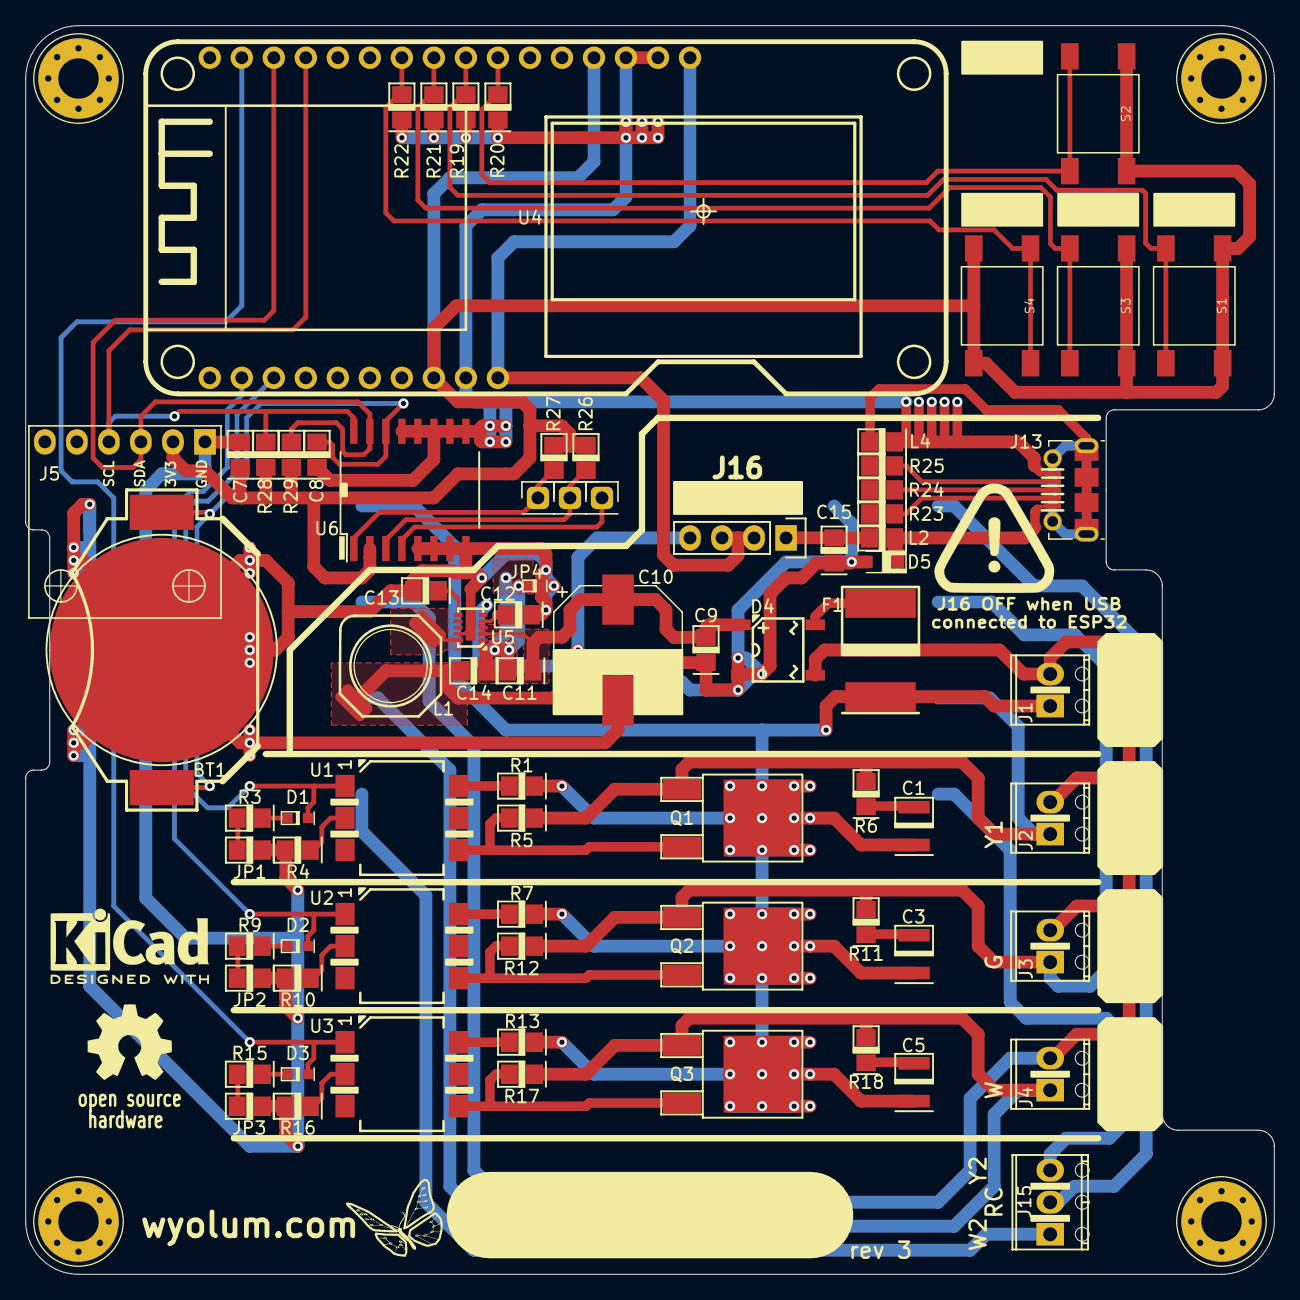
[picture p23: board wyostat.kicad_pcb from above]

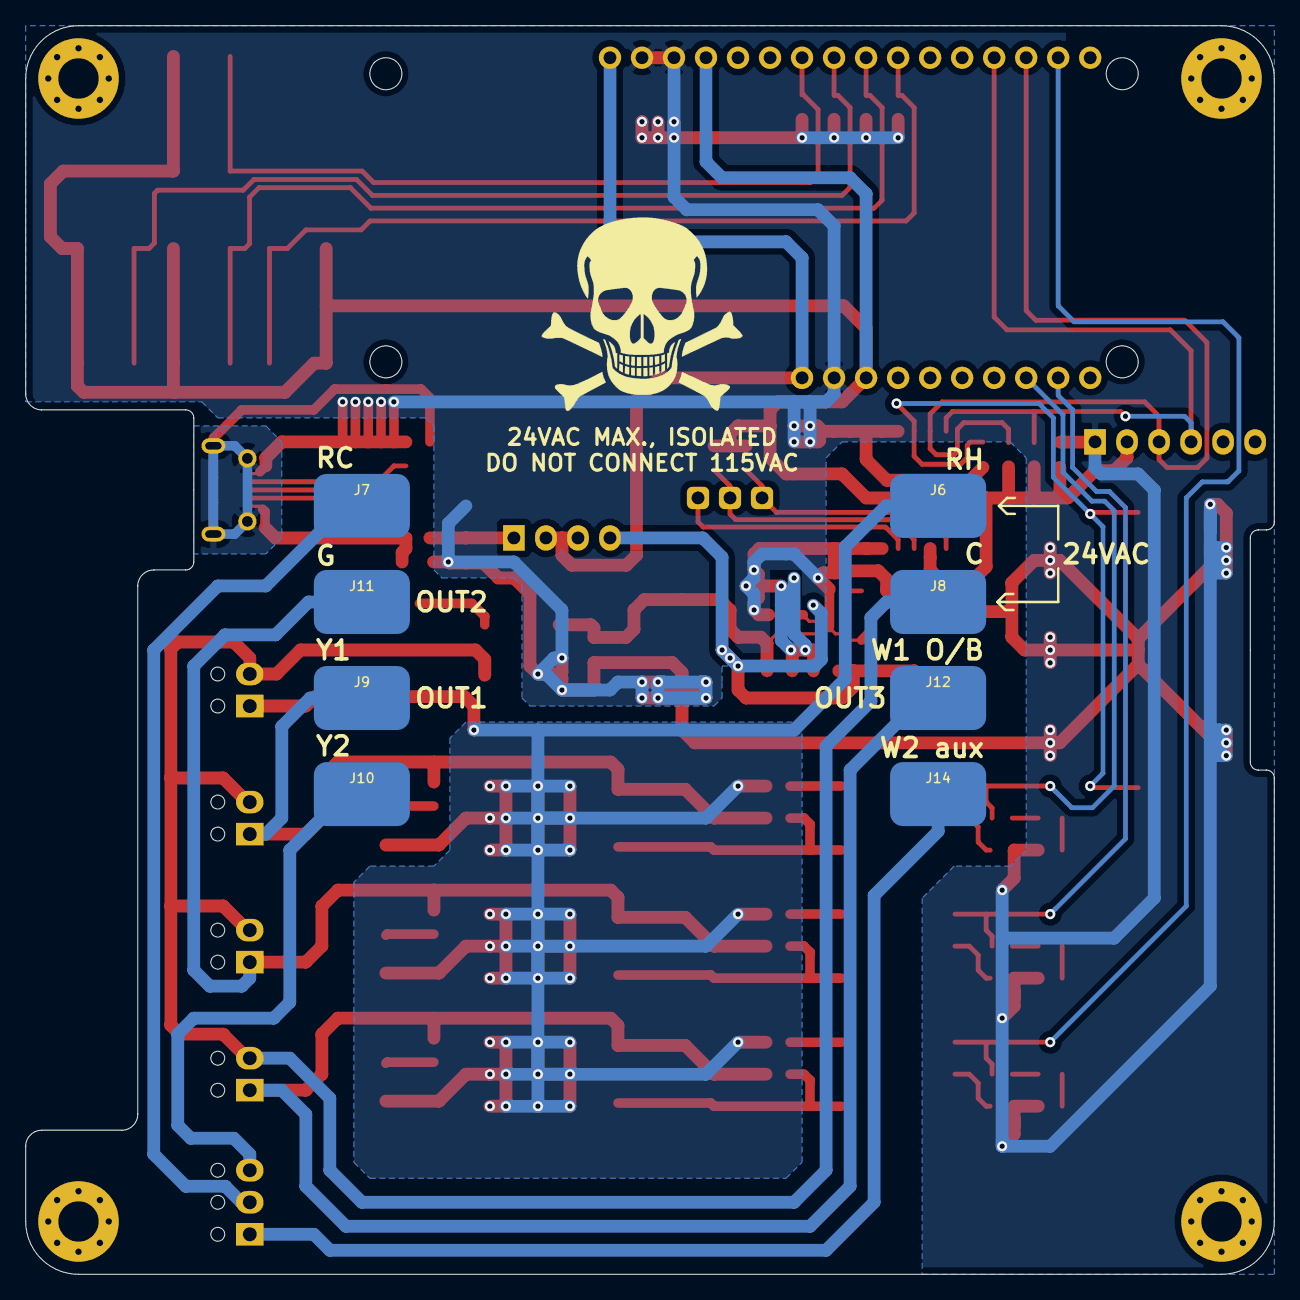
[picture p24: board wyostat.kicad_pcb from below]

Board: 2 copper layers, 99.1 x 99.1 mm, 93 parts (9 on the bottom side), 54 nets.

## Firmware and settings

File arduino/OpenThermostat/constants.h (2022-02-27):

#define INCR 15
#define DECR 12
#define MODE 14
#define ENTER 13
#define CH1 26
#define CH2 25
#define CH3 16

#define furnaceSCR CH3
#define fanSCR CH2
#define acSCR CH1

#define TARGETTEMP_ADDR 40
#define AWAY_ADDR 41

#define LOWEST_TEMP 40
#define HIGHEST_TEMP 90
#define DEFAULT_TARGETTEMP 50
#define DEFAULT_SETTEMPHI 80
#define HILOGAP 4
#define AWAYMIN 50
#define AWAYMAX 90
#define MIN_CHANGE_DURATION (1 * 60)

#define PI 3.141592653589793

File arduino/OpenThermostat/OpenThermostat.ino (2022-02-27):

/*
 Basic ESP32 MQTT example

 This sketch demonstrates the capabilities of the pubsub library in combination
 with the ESP8266 board/library.

 It connects to an MQTT server then:
  - publishes "hello world" to the topic "outTopic" every two seconds
  - subscribes to the topic "inTopic", printing out any messages
    it receives. NB - it assumes the received payloads are strings not binary
  - If the first character of the topic "inTopic" is an 1, switch ON the ESP Led,
    else switch it off

 It will reconnect to the server if the connection is lost using a blocking
 reconnect function. See the 'mqtt_reconnect_nonblocking' example for how to
 achieve the same result without blocking the main loop.



*/

#include <DNSServer.h>
#include <EEPROM.h>
#include <WiFiManager.h>
#include <NTPClient.h>
#include <TimeLib.h>
#include <EEPROM.h>
#include <EEPROMAnything.h>
#include <HTTPClient.h>
#include <PubSubClient.h>
#include <Wire.h>  // Only needed for Arduino 1.6.5 and earlier
#include <credentials.h>
#include "RTClib.h"
#include "SparkFunTMP102.h"
#include "SSD1306.h" // alias for `#include "SSD1306Wire.h"`
#include "icons.h"
#include "get_time.h"

// Update these with values suitable for your network.

#include "constants.h"

struct config_t{
  int timezone;
  uint8_t brightness;
  uint8_t display_idx;
  bool factory_reset;
  bool use_wifi;
  bool use_ip_timezone;
  uint8_t mqtt_ip[4];
  bool flip_display;
  uint32_t last_tz_lookup; // look up tz info every Sunday at 3:00 AM
  uint8_t solid_color_rgb[3];
  bool use_ntp_time;
  bool wifi_reset;
  uint8_t faceplate_idx;
} my_config;


void publish_int(char* topic, int val);
void publish_off_on(char* topic, int val);
void publish_bool(char* topic, bool val);
void setup_pins();
void setup_wifi();
void setup_temp();
void setup_display();
void mqtt_callback(char* topic, byte* payload, unsigned int length);
void mqtt_connect();
void mqtt_reconnect();
void displayTemp();

WiFiManager wifiManager;

//Adafruit_SSD1306  display(0x3c, 5, 4);
SSD1306  display(0x3c, 5, 4);
void drawTick(int16_t x0, int16_t y0, int16_t radius, double theta_deg, double length){
  double theta = theta_deg * PI / 180;
  double x1, x2, y1, y2;
  
  x1 = (radius - length) * cos(theta) + x0;
  y1 = -(radius - length) * sin(theta) + y0;
  x2 = (radius - 1) * cos(theta) + x0;
  y2 = -(radius - 1) * sin(theta) + y0;
  display.drawLine(x1, y1, x2, y2);
}

void arc_helper(int x0, int y0, int x, int y, int theta0_deg, int theta1_deg){
  double theta0 = theta0_deg * PI / 180;
  double theta1 = theta1_deg * PI / 180;
  double theta = atan2(-y + y0, x - x0);
  bool good0, good1, good2;
  good0 = theta0 <= theta - 2 * PI && theta - 2 * PI <= theta1;
  good1 = theta0 <= theta && theta <= theta1;
  good2 = theta0 <= theta + 2 * PI && theta + 2 * PI <= theta1;
  
  if(good0 || good1 || good2){
    display.setPixel(x, y);
  }
}

void drawArc(int16_t x0, int16_t y0, int16_t radius, double theta0_deg, double theta1_deg){
  int16_t x = 0, y = radius;
  int16_t dp = 1 - radius;
  if(theta0_deg > theta1_deg){
    int16_t swp = theta0_deg;
    theta0_deg = theta1_deg;
    theta1_deg = swp;
  }
  do {
    if (dp < 0)
      dp = dp + 2 * (++x) + 3;
    else
      dp = dp + 2 * (++x) - 2 * (--y) + 5;
    arc_helper(x0, y0, x0 + x, y0 + y, theta0_deg, theta1_deg);
    arc_helper(x0, y0, x0 - x, y0 + y, theta0_deg, theta1_deg);
    arc_helper(x0, y0, x0 + x, y0 - y, theta0_deg, theta1_deg);
    arc_helper(x0, y0, x0 - x, y0 - y, theta0_deg, theta1_deg);
    arc_helper(x0, y0, x0 + y, y0 + x, theta0_deg, theta1_deg);
    arc_helper(x0, y0, x0 - y, y0 + x, theta0_deg, theta1_deg);
    arc_helper(x0, y0, x0 + y, y0 - x, theta0_deg, theta1_deg);
    arc_helper(x0, y0, x0 - y, y0 - x, theta0_deg, theta1_deg);
  } while (x < y);
  
  arc_helper(x0, y0, x0 + radius, y0, theta0_deg, theta1_deg);
  arc_helper(x0, y0, x0, y0 + radius, theta0_deg, theta1_deg);
  arc_helper(x0, y0, x0 - radius, y0, theta0_deg, theta1_deg);
  arc_helper(x0, y0, x0, y0 - radius, theta0_deg, theta1_deg);
}

int count = 0;
float localtemp = 50.;
int last_temp = 0;

WiFiClient espClient;
PubSubClient mqtt_client(espClient);
long lastMsg = 0;
char msg[50] = "Hello Mosquitto!\n(from ESP32)";
TMP102 sensor0;
NTPClock ntp_clock;
DS3231Clock ds3231_clock;
DoomsdayClock doomsday_clock;
WiFiUDP ntpUDP;
NTPClient timeClient(ntpUDP, "us.pool.ntp.org", 0, 60000); //Default

bool furnace_state = false;
bool ac_state = false;
bool fan_state = false;
bool away;

// this is a typedef for topic callback funtions
typedef void (* TopicCallback_p)(byte* payload, unsigned int length);
struct TopicListener{
  char topic[50]; // topic string
  TopicCallback_p callback_p; // action
};

int bytes2int(byte* payload, unsigned int length){
  char str_payload[length + 1];
  for (int i = 0; i < length; i++) {
    str_payload[i] = (char)payload[i];
  }
  str_payload[length] = 0;
  return String(str_payload).toInt();
}

bool bytes2bool(byte* payload, unsigned int length){
  bool out = false;
  if(length > 0){
    out = payload[0] == 't';
  }
  return out;
}

uint8_t targettemps[2] = {60, 68};
uint8_t targettimes[2] = { 6, 22};
char hvacmode[50] = "heating";

int get_target_index(){
  uint8_t hh = ds3231_clock.hours();
  uint8_t out;
  if(hh < targettimes[0]){
    out = 0;
  }
  else if(hh < targettimes[1]){
    out = 1;
  }
  else{
    out = 0;
  }
  return out;
}
 
uint8_t get_targettemp(){
  uint8_t index = get_target_index();
  return targettemps[index];
}

uint8_t set_targettemp(uint8_t t){
  uint8_t index = get_target_index();
  targettemps[index] = t;
}

void _targettemp(int temp){
  if(LOWEST_TEMP <= temp && temp <= HIGHEST_TEMP){
    if(temp != get_targettemp()){
      set_targettemp(temp);
      displayTemp();
      EEPROM.write(TARGETTEMP_ADDR, temp);
      EEPROM.commit();
    }
  }
}

void targettemp_cb(byte *payload, unsigned int length){
  String str_temp;
    
  Serial.print("Set temp cb: ");
  Serial.println(bytes2int(payload, length));
  _targettemp(bytes2int(payload, length));  
}

void away_cb(byte *payload, unsigned int length){
  String str_temp;
  bool tmp = bytes2bool(payload, length);
  if(tmp != away){
    away = tmp;
    EEPROM.write(AWAY_ADDR, away);
    EEPROM.commit();
    displayTemp();
  }

  Serial.print("Set away cb: ");
  Serial.println(away);
}

void requesttemp_cb(byte *payload, unsigned int length){
  Serial.println("Request temp cb.");
  Serial.print("Sending:");
  Serial.println(localtemp);
  publish_hvac_state();
}

void requesttargettemp_cb(byte *payload, unsigned int length){
  Serial.println("Request target temp cb.");
  Serial.print("Sending:");
  Serial.println(get_targettemp());
  publish_hvac_state();
}

void requestmode_cb(byte *payload, unsigned int length){
  Serial.println("Request mode cb.");
  Serial.print("Sending:");
  Serial.println(hvacmode);
  mqtt_client.publish("wyostat.hvacmode", hvacmode);  
  publish_hvac_state();
}

void publish_hvac_state(){
  char *state;
  if(ac_state){
    state = "cooling";
  }
  else if(furnace_state){
    state = "heating";
  }
  else{
    state = "off";
  }
  Serial.print("Sending:");
  Serial.println(state);
  mqtt_client.publish("wyostat.hvac_state", state);
  publish_bool("wyostat.away", away);  
  publish_int("wyostat.temp", localtemp);
  publish_int("wyostat.targettemp", get_targettemp());
}
void requeststate_cb(byte *payload, unsigned int length){
  Serial.println("Request state cb.");
  publish_hvac_state();
}

void hvacmode_cb(byte *payload, unsigned int length){
  for(int i = 0; i < length; i++){
    hvacmode[i] = (char)payload[i];
  }
  hvacmode[length] = 0;
  Serial.print("wyostat.hvacmode: ");
  Serial.println(hvacmode);
}

int n_topic_listeners = 6;
const int MAX_TOPIC_LISTENERS = 50;

TopicListener targettemp_listener = {"wyostat.targettemp", targettemp_cb};
TopicListener away_listener = {"wyostat.away", away_cb};
TopicListener requesttemp_listener = {"wyostat.requesttemp", requesttemp_cb};
TopicListener requesttargettemp_listener = {"wyostat.requesttargettemp", requesttargettemp_cb};
TopicListener requestmode_listener = {"wyostat.requeststate", requestmode_cb};
TopicListener requeststate_listener = {"wyostat.requeststate", requeststate_cb};
TopicListener hvacmode_listener = {"wyostat.hvacmode", hvacmode_cb};

TopicListener *TopicListeners[MAX_TOPIC_LISTENERS] = {&targettemp_listener,
						      &away_listener,
						      &requesttemp_listener,
						      &requesttargettemp_listener,
						      &requestmode_listener,
						      &hvacmode_listener,
						      &requeststate_listener,
						      };


// return json value for name identified (or "not found")
String jsonLookup(String s, String name){
  String out;
  int start, stop;
  
  name = String("\"") + name + String("\""); // add bounding quotes

  start = s.indexOf(name);
  if(start < 0){
    out = String("not found");
  }
  else{
    start +=  name.length() + 2;
    stop = s.indexOf('"', start);
    out = s.substring(start, stop);
  }
  return out;
}

void set_timezone_from_ip(){

  HTTPClient http;
  String payload;
  
  Serial.print("[HTTP] begin...\n");
  // configure traged server and url
  //http.begin("https://www.howsmyssl.com/a/check", ca); //HTTPS
  // http.begin("http://example.com/index.html"); //HTTP

  //http.begin("https://timezoneapi.io/api/ip");// no longer works!
  String url = String("https://www.wyolum.com/utc_offset/utc_offset.py") +
    String("?refresh=") + String(millis()) +
    String("&localip=") +
    String(WiFi.localIP()[0]) + String('.') + 
    String(WiFi.localIP()[1]) + String('.') + 
    String(WiFi.localIP()[2]) + String('.') + 
    String(WiFi.localIP()[3]) + String('&') +
    String("macaddress=") + WiFi.macAddress() + String('&') + 
    String("dev_type=ClockIOT");
  Serial.println(url);
  http.begin(url);
  
  Serial.print("[HTTP] GET...\n");
  // start connection and send HTTP header
  int httpCode = http.GET();
  
  // httpCode will be negative on error
  //httpCode = -1; // force error
  if(httpCode < 0){
    http.end();
    url = String("https://ipapi.co/json/?key=");
    Serial.print("Using backup url:");
    Serial.println(url + "<SECRET KEY>");
    http.begin(url + ipapikey);
  
    Serial.print("[HTTP] GET...\n");
    // start connection and send HTTP header
    httpCode = http.GET();
  }
  payload = http.getString();
  if(httpCode > 0) {
    // HTTP header has been send and Server response header has been handled
    Serial.printf("[HTTP] GET... code: %d\n", httpCode);
    
    // file found at server
    //String findme = String("offset_seconds");
    if(httpCode == HTTP_CODE_OK) {
      Serial.print("payload:");
      Serial.println(payload);
      payload.replace(" ", "");
      String offset_str = jsonLookup(payload, String("utc_offset"));
      int hours = offset_str.substring(0, 3).toInt();
      int minutes = offset_str.substring(3, 5).toInt();
      if(hours < 0){
	minutes *= -1;
      }
      int offset = hours * 3600 + minutes * 60;

      String utc_str =jsonLookup(payload, String("utc"));
      Serial.print("  UTC:"); Serial.println(utc_str);
      if(!utc_str.equals("not found")){
	uint32_t local = utc_str.toInt() + offset;
	Serial.print("Local:");Serial.println(local);
	ds3231_clock.set(local);
	Serial.println("local set");
      }
      Serial.println("is NTP Alive?");
      if(false && doomsday_clock.master->initialized){
	Serial.println("NTP is clock alive!");
      }
      else{
	Serial.println("No NTP, fall back to DS3231");
      }
      Serial.println();
      Serial.print("timezone_offset String:");
      Serial.println(offset_str);
      Serial.print("timezone_offset:");
      Serial.println(offset);
      //set_timezone_offset(offset, gmt);
      //my_config.last_tz_lookup = doomsday_clock.gmt();
      //saveSettings();
    }
    else{
      Serial.println("No timezone found");
      Serial.println("Payload:");
      Serial.println(payload);
    }
  }
}

void loadSettings()
{
  byte tmp;

  //targettemp = EEPROM.read(TARGETTEMP_ADDR);
  //if(targettemp == 255){
  //  targettemp = DEFAULT_TARGETTEMP;
  // }
  tmp = EEPROM.read(AWAY_ADDR);
  if(tmp == 255){
    away = false;
  }
  else{
    away = (bool)tmp;
  }
}

unsigned int last_furnace_state_change = 0;
void set_furnace(bool state){
  if(state != furnace_state &&
     ds3231_clock.now() - last_furnace_state_change > MIN_CHANGE_DURATION){
    Serial.print("Setting Furnace:");
    Serial.println(furnace_state);
    furnace_state = state;
    digitalWrite(furnaceSCR, state);
    last_furnace_state_change = ds3231_clock.now();
    publish_off_on("wyostat.furnace_state", furnace_state);
    publish_hvac_state();
    display.setColor(BLACK);
    display.fillRect(16, 16, 32, 32);
    display.setColor(WHITE);
    if(furnace_state){
      display.drawXbm(16, 16, fire_width, fire_height, fire_bits);
    }
    display.display();
  }
}

void set_ac(bool state){
  if(state != ac_state){
    ac_state = state;
    digitalWrite(acSCR, state);
    Serial.print("Setting AC:");
    publish_off_on("wyostat.furnace_state", ac_state);
    publish_hvac_state();
    display.setColor(BLACK);
    display.fillRect(16, 16, 32, 32);
    display.setColor(WHITE);
    if(ac_state){
      display.drawXbm(16, 16, flake_width, flake_height, flake_bits);
    }
    display.display();
  }
}

void set_fan(bool state){
  if(state != fan_state){
    Serial.print("Setting Fan:");
    if(state){
      Serial.println(" On");
      mqtt_client.publish("wyostat.fan_state", "1");
    }
    else{
      Serial.println(" Off");
      mqtt_client.publish("wyostat.fan_state", "0");
    }
    fan_state = state;
    digitalWrite(fanSCR, state);
  }
}

void setup() {
  String str;
  
  pinMode(BUILTIN_LED, OUTPUT);     // Initialize the BUILTIN_LED pin as an output
  Wire.begin(5, 4);
  Serial.begin(115200);
  setup_pins();
  setup_wifi();
   setup_temp();
  
  uint8_t mqtt_server[4] = {192, 168, 7, 159};
  mqtt_client.setServer(mqtt_server, 1883);
  mqtt_client.setCallback(mqtt_callback);

  EEPROM.begin(512);
  loadSettings();
  setup_rtc();
  setup_display();
  if(true){ // test icons?
////////////////////////////////////////////////////////////////////////////////
  // TEST  (works !!!)
    display.clear();
    display.drawXbm(16, 16, fire_width, fire_height, fire_bits);
    display.display();
    delay(1000);

    display.clear();
    display.drawXbm(16, 16, flake_width, flake_height, flake_bits);
    display.display();
    delay(1000);

    display.clear();
    display.drawXbm(16, 16, leaf_width, leaf_height, leaf_bits);
    display.display();
    delay(1000);
////////////////////////////////////////////////////////////////////////////////
  }
  set_timezone_from_ip();
  mqtt_connect();
  ntp_clock.setup(&timeClient);
  ntp_clock.setOffset(0);
  doomsday_clock.setup(&ntp_clock, &ds3231_clock);
  
  Serial.println(ds3231_clock.now());
}

void setup_rtc(){
  //ds3231_clock.begin();
  //ds3231_clock.adjust(DateTime(2022, 2, 13, 15, 17, 0));
}

void setup_display(){
  // Initialising the UI will init the display too.
  display.init();

  display.flipScreenVertically();
  display.setFont(ArialMT_Plain_10);
  display.clear();
  display.display();

  displayTemp();
}
void font_demo(){
  // Font Demo1
  // create more fonts at http://oleddisplay.squix.ch/
  display.clear();
  display.setTextAlignment(TEXT_ALIGN_LEFT);
  display.setFont(ArialMT_Plain_10);
  display.drawString(0, 0, "Hello world");
  display.display(); delay(1000);
  display.setFont(ArialMT_Plain_16);
  display.drawString(0, 10, "Hello world");
  display.display(); delay(1000);
  display.setFont(ArialMT_Plain_24);
  display.drawString(0, 26, "Hello world");
  display.display(); delay(1000);
}

void xbmDemo(){
  // test 1
  // display.drawXbm(0, -30, xbm_width, xbm_height, xbm_bits);
  // display.invertDisplay();

  // test 2
  display.drawXbm(0, 0, leaf_width, leaf_height, leaf_bits);
  display.drawXbm(0, 32, flake_width, flake_height, flake_bits);
  display.drawXbm(32, 32, fire_width, fire_height, fire_bits);

  return;
}

void displayTemp(){
  double theta_deg;

  int x0 = 128 - 32 - 1;
  int y0 = 32;
  int y;
  
  int theta0, theta1;
  String tempstr;
  double gain = 315 / 50.;
  
  if (get_targettemp() < LOWEST_TEMP){
    theta1 = gain * (80 - LOWEST_TEMP);
  }
  else{
    theta1 = gain * (80 - get_targettemp());
  }
  if (get_targettemp() > HIGHEST_TEMP){
    theta1 = gain * (80 - HIGHEST_TEMP);
  }
  else{
    theta1 = gain * (80 - get_targettemp());
  }
  if (localtemp < LOWEST_TEMP){
    theta0 = gain * (80 - LOWEST_TEMP);
  }
  else{
    theta0 = gain * (80 - localtemp);
  }
  if (localtemp > HIGHEST_TEMP){
    theta0 = gain * (80 - HIGHEST_TEMP);
  }
  else{
    theta0 = gain * (80 - localtemp);
  }
  if(away){
    theta1 = theta0 + 2;
    theta0 = theta1 - 3;
  }
  display.setColor(BLACK); // clear right half of display
  display.fillRect(64, 0, 64, 64);
  display.setColor(WHITE);

  drawArc(x0, y0, 31, -67, 247);
  drawArc(x0, y0, 32, -67, 247);
  drawArc(x0, y0, 33, -67, 247);
	     
  drawArc(x0, y0, 27, theta0, theta1);
  drawArc(x0, y0, 26, theta0, theta1);

  int n_tick = 6;
  for(int i=0; i<n_tick; i++){
    theta_deg = (int)(-67.5 + 315. / (n_tick - 1) * i);
    //drawTick(x0, y0, 32, theta_deg, 5);
  }
  
  // display target temp
  display.setTextAlignment(TEXT_ALIGN_CENTER);
  if(away){
    display.setFont(ArialMT_Plain_16);
    tempstr = String("AWAY");
  }
  else{
    display.setFont(ArialMT_Plain_24);
    tempstr = String(get_targettemp());
  }
  display.drawString(x0, y0 - 12, tempstr.c_str());

  // display local temp
  display.setFont(ArialMT_Plain_10);
  display.setTextAlignment(TEXT_ALIGN_CENTER);
  tempstr = String((int)localtemp);
  if(localtemp < get_targettemp()){
    y = y0 - 24;
  }
  else{
    y = y0 + 12;
  }
  display.drawString(x0, y, tempstr.c_str());

  /*
  if(furnace_state){
    display.setColor(BLACK);
    display.fillRect(16, 16, 32, 32);
    display.setColor(WHITE);
    display.drawXbm(16, 16, fire_width, fire_height, fire_bits);
    display.display();
  }
  if(ac_state){
    display.setColor(BLACK);
    display.fillRect(16, 16, 32, 32);
    display.setColor(WHITE);
    display.drawXbm(16, 16, flake_width, flake_height, flake_bits);
    display.display();
    }
  */
  display.display();
}

  
void setup_pins(){
  pinMode(furnaceSCR,OUTPUT);
  pinMode(fanSCR,OUTPUT);
  pinMode(acSCR,OUTPUT);
  digitalWrite(furnaceSCR,LOW);
  digitalWrite(fanSCR,LOW);
  digitalWrite(acSCR,LOW);
}

void setup_temp(){
  sensor0.begin();
  // set the Conversion Rate (how quickly the sensor gets a new reading)
  //0-3: 0:0.25Hz, 1:1Hz, 2:4Hz, 3:8Hz
  sensor0.setConversionRate(2);
  //set Extended Mode.
  //0:12-bit Temperature(-55C to +128C) 1:13-bit Temperature(-55C to +150C)
  sensor0.setExtendedMode(0);
  localtemp = sensor0.readTempF();
}
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
void loop() {
  float temp = localtemp;
  int sensor_temp;
  long now;
  String str_temp;
  String topic = String("wyostat.temp");

  if(loop_counter++ % 1000 == 0){
    sensor0.wakeup();
    sensor_temp =  sensor0.readTempF();
    if(0 < sensor_temp && sensor_temp < 200){
      localtemp = 0.9999 * localtemp + 0.0001 * sensor_temp;
    }
    //Serial.println(localtemp);
  }
  else{
    delay(1);
  }
  //localtemp = 73; // previous line breaks display!!
  
  // Turn sensor on to start temperature measurement.
  // Current consumtion typically ~10uA.
  /*
  */
  if (!mqtt_client.connected()) {
    mqtt_reconnect();
  }
  mqtt_client.loop();
  if(hvacmode[0] == 'h'){ // heating mode
    set_ac(false);
    if(away){
      if(localtemp < AWAYMIN - HILOGAP / 2){
	set_furnace(true);
      }
      else if(localtemp > AWAYMIN + HILOGAP / 2){
	set_furnace(false);
      }
      set_fan(furnace_state);
    }
    else{
      if (int(localtemp) > get_targettemp() - HILOGAP / 2){ // too hot
	set_furnace(false);
      }
      else if(int(localtemp) < get_targettemp() + HILOGAP / 2){ // too cold
	set_furnace(true);
      }
      else{ // just right
      }
      set_fan(furnace_state);      
    }
  }
  else if(hvacmode[0] == 'c'){ // cooling mode
    set_furnace(false);
    if(away){
      if(localtemp > AWAYMAX){
	set_fan(true);
	set_ac(true);
      }
      else if(localtemp < AWAYMAX - HILOGAP){
	set_fan(false);
	set_ac(false);
      }
    }
    else{
      if (int(localtemp) > get_targettemp()){ // too hot
	set_ac(true);
	set_fan(true);
      }
      else if (int(localtemp) <= get_targettemp() - HILOGAP){ // too cold
	set_ac(false);
	set_fan(false);
      }
      else{ // just right
      }
    }
  }
  else{
    set_ac(false);
    set_furnace(false);
    set_fan(false);
  }

  if((int)temp != int(localtemp)){
    displayTemp();
  }
  now = millis();
  if (now - lastMsg > 2000) {
    lastMsg = now;
    if(temp != last_temp){
      last_temp = temp;
      Serial.print("temp: ");
      Serial.println(temp);
      str_temp = String(temp);
      mqtt_client.publish(topic.c_str(), str_temp.c_str());
    }
  }

  static int loop_counter = 0;
  if(loop_counter++ % 10000 == 0){
    Serial.print(ds3231_clock.hours());
    Serial.print(" ");
    Serial.print(get_targettemp());
    Serial.print(" ");
    Serial.print(targettemps[0]);
    Serial.print(" ");
    Serial.print(targettemps[1]);
    Serial.print(" ");
    if(ds3231_clock.now() - last_furnace_state_change < MIN_CHANGE_DURATION){
      Serial.print(ds3231_clock.now() - last_furnace_state_change);
    }
    Serial.println();
  }
}

void set_timezone_offset(int32_t offset, NTPClock ntp_clock){
  my_config.timezone = offset % 86400;
  saveSettings();
  if(my_config.use_wifi){
    ntp_clock.setOffset(my_config.timezone);
  }
}

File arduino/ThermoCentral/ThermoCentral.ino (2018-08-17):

/**
 * The MIT License (MIT)
 *
 * Copyright (c) 2016 by Daniel Eichhorn
 * Copyright (c) 2016 by Fabrice Weinberg
 *
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
 */

#include "config.h"
#include <Wire.h>  // Only needed for Arduino 1.6.5 and earlier
#include "RTClib.h"
#include <EEPROM.h>
#include "SparkFunTMP102.h"
#include "SSD1306.h" // alias for `#include "SSD1306Wire.h"`

#define INCR 15
#define DECR 12
#define MODE 14
#define ENTER 13
#define CH1 26
#define CH2 25
#define CH3 16

bool channel_status[3];

RTC_DS3231 rtc;

// set up feeds
AdafruitIO_Feed *livingroomtemp = io.feed("LivingRoomTemp");
AdafruitIO_Feed *setTempLo = io.feed("wyostat.settemplo");
AdafruitIO_Feed *setTempHi = io.feed("wyostat.settemphi");
AdafruitIO_Feed *furnace_state = io.feed("wyostat.furnace-state");
AdafruitIO_Feed *ac_state = io.feed("wyostat.ac-state");

int living = 0;
int bedroom =0;
int settemperature_lo = 55;
int settemperature_hi = 80;

 // is the furnace/AC/fan on or off
int furnacestate = 0;
int acstate = 0;
int fanstate = 0;

// temp gap for hysteresis control
float  tempgap = 2.0L;
 //time
 DateTime now;
 void handleButtons();
#define furnaceSCR CH3
#define fanSCR CH2
#define acSCR CH1
 
// Include the UI lib
#include "OLEDDisplayUi.h"

// Include custom images
#include "images.h"

// Use the corresponding display class:


// Initialize the OLED display using Wire library
SSD1306  display(0x3c, 5, 4);
TMP102 sensor0(0x48);

OLEDDisplayUi ui     ( &display );
String livingroomtitle = String("LivingRoom");
String bedroomtitle = String("Time");
String currentRoom = bedroomtitle;
void roomOverlay(OLEDDisplay *display, OLEDDisplayUiState* state) {
  display->setTextAlignment(TEXT_ALIGN_RIGHT);
  display->setFont(ArialMT_Plain_10);
  display->drawString(128, 0, currentRoom);
}

void drawFrame2(OLEDDisplay *display, OLEDDisplayUiState* state, int16_t x, int16_t y) {
  int minute = now.minute();
  int hour = now.hour();
  String ampmstr;
  String minutestr;
  if (hour >12){
    hour = hour - 12;
    ampmstr = " PM";
  }else
    ampmstr = " AM";
  if (minute < 10){
    minutestr = String("0")+String(minute);
  }else
  minutestr = String(minute);
  String timestring = String(hour) + String(":")+minutestr+ampmstr;
  String tempstring = String(living) + String("° F");
  currentRoom = bedroomtitle;
  display->setFont(ArialMT_Plain_24);
  display->setTextAlignment(TEXT_ALIGN_CENTER);
  display->drawString(60 + x, 25 + y, timestring);
  display->setFont(ArialMT_Plain_16);
  display->setTextAlignment(TEXT_ALIGN_LEFT);
  display->drawString(0+x,10+y,tempstring);
}

void drawFrame1(OLEDDisplay *display, OLEDDisplayUiState* state, int16_t x, int16_t y) {
  String livingroomstring = String(living) + String("° F");
  String setstring = String(settemperature_lo) + String("-") + String(settemperature_hi) + String("° F");
  String statusstring;
  if (furnacestate){
    statusstring = String("Heat");
  }
  else if(acstate){
    statusstring = String("Cool");
  }
  else if(fanstate){
    statusstring = String("Fan");
  }
  else{
    statusstring = String("Off");
  }
  
  currentRoom = livingroomtitle;
  display->setFont(ArialMT_Plain_24);
  display->setTextAlignment(TEXT_ALIGN_CENTER);
  display->drawString(80 + x, 15 + y, livingroomstring);
  display->setFont(ArialMT_Plain_16);
  display->setTextAlignment(TEXT_ALIGN_LEFT);
  display->drawString(0+x,0+y,setstring);
  display->drawString(58 + x, 45 + y, statusstring);
}



void drawFrame5(OLEDDisplay *display, OLEDDisplayUiState* state, int16_t x, int16_t y) {

}

// This array keeps function pointers to all frames
// frames are the single views that slide in
FrameCallback frames[] = { drawFrame1, drawFrame2 };

// how many frames are there?
int frameCount = 1;

// Overlays are statically drawn on top of a frame eg. a clock
OverlayCallback overlays[] = { roomOverlay};
int overlaysCount = 1;

void setup() {
  Serial.begin(115200);
  Serial.println();
  Serial.println();
  pinMode(furnaceSCR,OUTPUT);
  pinMode(fanSCR,OUTPUT);
  pinMode(acSCR,OUTPUT);
  digitalWrite(furnaceSCR,LOW);
  digitalWrite(fanSCR,LOW);
  digitalWrite(acSCR,LOW);
  sensor0.begin();
  // set the Conversion Rate (how quickly the sensor gets a new reading)
  //0-3: 0:0.25Hz, 1:1Hz, 2:4Hz, 3:8Hz
  sensor0.setConversionRate(2);
  //set Extended Mode.
  //0:12-bit Temperature(-55C to +128C) 1:13-bit Temperature(-55C to +150C)
  sensor0.setExtendedMode(0);
	// The ESP is capable of rendering 60fps in 80Mhz mode
	// but that won't give you much time for anything else
	// run it in 160Mhz mode or just set it to 30 fps

  // prevent page automatic turns.
  ui.disableAutoTransition();


  // these are not needed, unless we re enable display changing.
  ui.setTargetFPS(30);
  //ui.setTimePerFrame(20000);
  ui.transitionToFrame(0);

	// Customize the active and inactive symbol
  //ui.setActiveSymbol(activeSymbol);
  //ui.setInactiveSymbol(inactiveSymbol);

  // You can change this to
  // TOP, LEFT, BOTTOM, RIGHT
  //ui.setIndicatorPosition(BOTTOM);

  // Defines where the first frame is located in the bar.
  //ui.setIndicatorDirection(LEFT_RIGHT);

  // You can change the transition that is used
  // SLIDE_LEFT, SLIDE_RIGHT, SLIDE_UP, SLIDE_DOWN
  //ui.setFrameAnimation(SLIDE_UP);

  // Add frames
  //ui.setFrames(frames, frameCount);

  // Add overlays
  //ui.setOverlays(overlays, overlaysCount);

  // Initialising the UI will init the display too.
  ui.init();

  display.flipScreenVertically();
  // connect to adafruit.io
  io.connect();
  //bedroomtemp->onMessage(handleBedroom);
  livingroomtemp->onMessage(handleLivingroom);
  setTempLo->onMessage(handleSetTempLo);
  setTempHi->onMessage(handleSetTempHi);
  //furnace->onMessage(handleFurnace);
    // wait for a connection
  while(io.status() < AIO_CONNECTED) {
    Serial.print(".");
    delay(500);
  }

  // we are connected
  Serial.println();
  Serial.println(io.statusText());

  EEPROM.begin(512);
  loadSettings();
   if (! rtc.begin()) {
    Serial.println("Couldn't find RTC");
    while (1);
  }

  if (rtc.lostPower()) {
    Serial.println("RTC lost power, lets set the time!");
    // following line sets the RTC to the date & time this sketch was compiled
    rtc.adjust(DateTime(F(__DATE__), F(__TIME__)));
    // This line sets the RTC with an explicit date & time, for example to set
    // January 21, 2014 at 3am you would call:
    // rtc.adjust(DateTime(2014, 1, 21, 3, 0, 0));
  }
  
  // dont draw display indicator
  //ui.disableIndicator();
  //ui.disableAllIndicators();
}
const uint8_t DEFAULT_SET_TEMP_LO = 55;
const uint8_t DEFAULT_SET_TEMP_HI = 80;
const uint8_t SET_TEMP_LO_ADDR = 0;
const uint8_t SET_TEMP_HI_ADDR = 1;
void loadSettings()
{
  settemperature_lo = EEPROM.read(SET_TEMP_LO_ADDR);
  if(settemperature_lo == 255){
    settemperature_lo = DEFAULT_SET_TEMP_LO;
  }
  settemperature_hi = EEPROM.read(SET_TEMP_HI_ADDR);
  if(settemperature_hi == 255){
    settemperature_hi = DEFAULT_SET_TEMP_HI;
  }
    
}
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

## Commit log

2017-12-30 remove static copy of esp32 files
2017-12-30 try to checkin all the hardware files we need
    [default.csv, minimal.csv]
2017-12-31 add prototype bom
2018-03-12 initial kicad setup kicad
    [MicroUSB-B_Molex_105017-0001.step, cap_0805_2012M.step, cap_2917_7343M.step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]
2018-03-12 kicad schematic, WIP
    [wyostat.sch]
2018-03-13 schematic WIP
    [0ZCF.step, wyostat.sch]
2018-03-15 layou, WIP
    [wyostat.kicad_pcb, wyostat.sch]
2018-03-15 kicad PCB, WIP
    [Conn_Phoenix_MPT.step, SOT-428.step, SW_SPST_CK_KSCx.step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]
2018-03-16 kicad PCB, track layout
    [wyostat.kicad_pcb, wyostat.sch]
2018-03-17 PCB layout, WIP
    [wyostat.sch]
2018-03-18 initial board layout
    [D_SOD323.step, SOIC16_Wide.step, bat_2032_2.step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]
2018-03-19 adding pads for spring contacts
    [wyostat.kicad_pcb, wyostat.sch]
2018-03-19 Gerbers ready for OSHpark
    [cap_1210_3225M.step, pad_rect_smd.step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]
2018-03-20 increased clearances, added inverse text
    [wyostat-B.Cu.gbl, wyostat-B.Mask.gbs, wyostat-B.Paste.gbp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]
2018-03-20 added gerber zip
2018-03-20 improved silk legend
    [wyostat-B.Cu.gbl, wyostat-B.Mask.gbs, wyostat-B.Paste.gbp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]
2018-03-22 trying out an enclosure/front cover plate
2018-03-23 enclosure, WIP
    [header_F_1x10.step, wyostat_cover.stl]
2018-03-24 modified contact pad positions
    [Header_F16x2-54.step, Header_F_10x2_54.step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]
2018-03-24 enclosure WIP
2018-03-24 enclosure, first version, STL
    [header_F_1x10.step, wyostat_cover.stl]
2018-03-24 enclosure, buttons
    [wyostat.kicad_pcb, wyostat_buttons.stl]
2018-03-25 revised Butons STL
    [wyostat_buttons.stl]
2018-03-26 modified Paste layer. Fixed Coin Cell footprint
    [wyostat-B.Cu.gbl, wyostat-B.Mask.gbs, wyostat-B.Paste.gbp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]
2018-04-04 footprint corrections on PCB
    [rtc_ds3231.sch, wyostat.kicad_pcb, wyostat.sch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]
2018-04-05 PCB updated for 2nd round of prototype
    [rtc_ds3231.sch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]
2018-04-05 added Sparkfun TMP102 footprint and PCB edges modified
    [Pin_Header_Straight_1x06_Pitch2.54mm.step, pin_header_female_01x06.step, sparkfun_TMP102.fcstd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]
2018-04-06 3D printed case - added opening for temp sensor
    [wyostat.kicad_pcb, wyostat_cover.stl]
2018-06-11 prettified silk legend
    [cap_elco_10x10x10.step, rtc_ds3231.sch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]
2018-06-13 added details to Fabricate layer for assembly guide
    [wyostat.kicad_pcb]
2018-07-29 Added lo and hi settings for temperature control to allow control of AC and Furnace
2018-08-05 add esp32 mqtt example
2018-08-07 added wyostat messages to mqtt example
    [optocoupler_MOC_SMD.step, optocoupler_MOC_TH.step, optocoupler_MOC_smd.step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]
2018-09-02 added rev4 KiCAD folder, WIP
    [0ZCF.step, 21-0429B-L.step, 21-0429B-M.step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]
2018-11-19 testing display... not working
    [OpenThermostat.ino]
2018-11-20 debuggin display sensor compatibility
2018-11-22 re-compiled on Linux... using arduino 1.8.7, new libs seem required
2018-11-22 got temp to read by waking sensor prior to each read
2022-02-15 adding wyolum time service, getting compile errors
    [OpenThermostat.ino]
2022-02-27 added flow graph for node red

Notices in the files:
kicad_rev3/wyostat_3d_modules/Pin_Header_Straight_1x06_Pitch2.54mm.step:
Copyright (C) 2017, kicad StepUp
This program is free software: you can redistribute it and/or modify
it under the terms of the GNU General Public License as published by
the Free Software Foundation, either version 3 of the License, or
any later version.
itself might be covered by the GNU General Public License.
